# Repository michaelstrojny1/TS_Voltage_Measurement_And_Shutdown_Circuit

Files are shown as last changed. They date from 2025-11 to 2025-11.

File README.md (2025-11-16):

Built for Electric Car tractive system. Two circuits are included:
(1) Galvanically isolated low noise high voltage measurement circuit feeding voltage measurement to STM32 MCU. 
(2) Relay powered Shutdown Circuit discharging DC-Link (RC circuit initally at ~600V) to 60V in 3 seconds

Please read **Documentation.pdf** for calculations and further explanation

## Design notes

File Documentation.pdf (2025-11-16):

# TS Measurement & Discharge

Michael Strojny
Link to Altium Project (https://michael-strojny.365.altium.com/designs/B8E9C9AF-7C63-4BC2-A13C-E0917E1C21B7)

## 1.0 TS Measurement Circuit

### 1.0.1 Our Approach

The AMC1311B (https://www.ti.com/lit/ds/symlink/amc1311.pdf?HQS=dis-dk-null-digikeymode-dsf-pf-null-wwe&ts=1762965607737) takes in a voltage between 0 and 2V and outputs that voltage in differential pair form (i.e difference between pairs equals V ). Since our DC-link voltage is around , we
IN

600V
divide our voltage using a 301:1 ratio voltage divider; our top resistor is 6 MΩ and the bottom resistor is 20 kΩ. The MCU to which the differential pair feeds then re-scales the divided voltage back to the true value, “measuring” the DC-Link voltage.

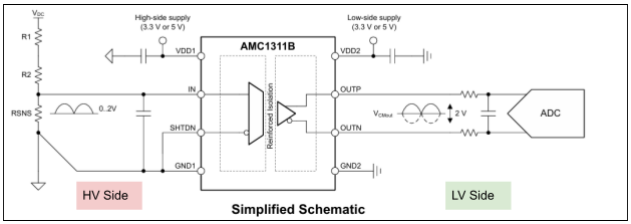
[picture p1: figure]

Figure 1 – AMC1311B + Schematic with Best Practices AMC1311B Datasheet (https://www.ti.com/lit/ds/symlink/amc1311.pdf?HQS=dis-dk-null-digikeymode-dsf-pf-null-wwe&ts=1762965607737)

The input of the AMC1311B is galvanically isolated from the output, which prevents dangerous high voltage from reaching our low voltage electronics. The AMC1311B clamps voltages above 2V. However, extra current still flows into the AMC1311B at higher input voltages. The AMC’s maximum input current is 10mA, yet the AMC impedance is ~1 gigaohm, meaning we are resilient even to large transients.

Notice that we require a 3.3 or 5V supply on both sides of the AMC1311B (pins VDD1 and VDD2). This power will come from the low voltage side. We power the high voltage side by connecting the low voltage power supply to the high voltage side using a 5VDC to 5VDC isolated converter NME0505DC. (https://www.murata.com/products/productdata/8807031111710/kdc-nme.pdf) This keeps both sides galvanically isolated. Note that the NME0505DC (https://www.murata.com/products/productdata/8807031111710/kdc-nme.pdf) requires at least 10% of its fully rated load (200 mA) to work properly.

The AMC1311B chops the input signal at a rate of 20Mhz meaning we need a couple picofarads of capacitance in parallel with the voltage divider feeding into the AMC to ensure we have enough current to supply each switch. The AMC also steals about 3.5 nA of current from our divider; it has 1 gigaohm impedance in parallel with the 20 kΩ; its effect on the voltage divider is negligible. Additional decoupling capacitors are also recommended for power supplies. See Figure 2.

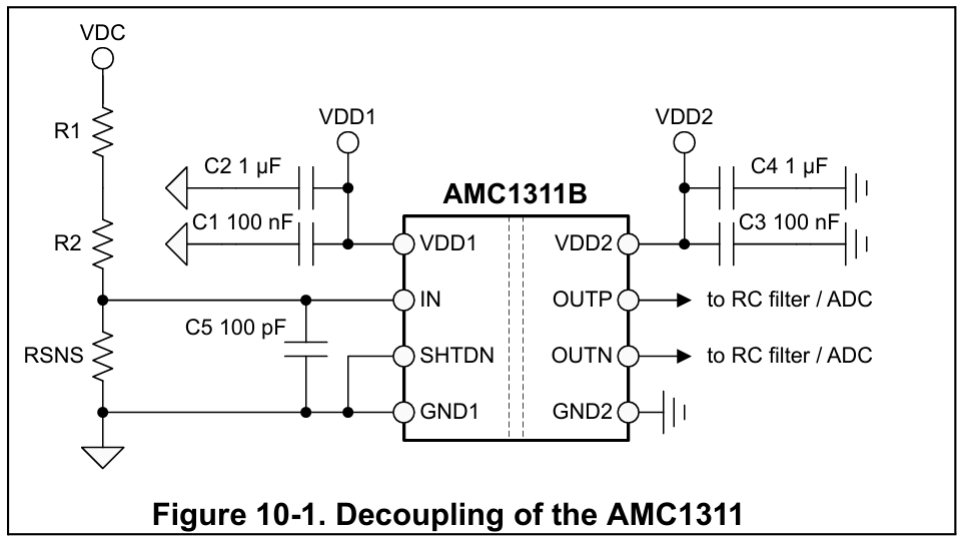
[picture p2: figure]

Figure 2 – Recommended AMC1311 Decoupling Capacitor Layout

Some STM32 MCUs accept differential pairs and some don't. If our MCU does not accept differential pairs, we can simply use an Op-Amp to get a 3.3V analog signal. See Figure 3 for an example on how to do this given by the datasheet, where “For most applications, R1 = R2 = R3 = R4 = 3.3 kΩ and C1 = C2 = 330 pF yields good performance”. More information can be found in 18-Bit, 1MSPS Data Acquisition Block (DAQ) (https://www.ti.com/lit/ug/slau515a/slau515a.pdf?ts=1763006584930)

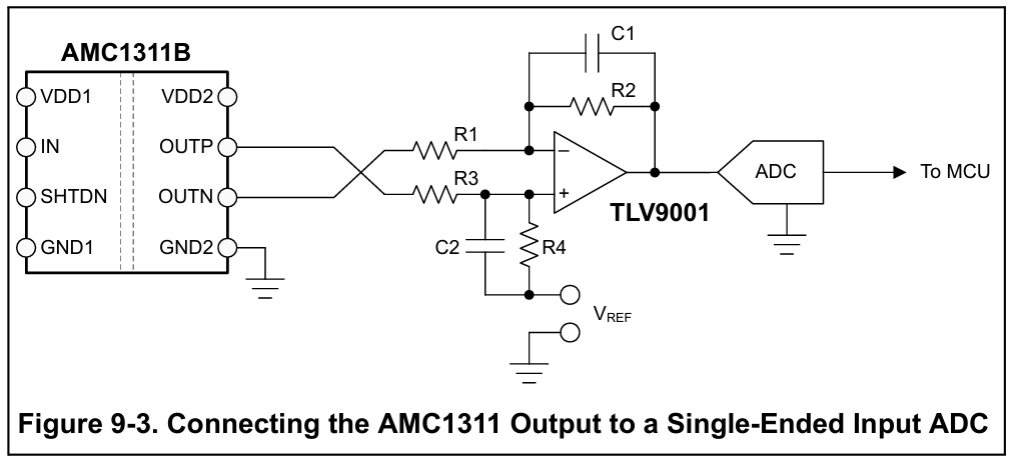
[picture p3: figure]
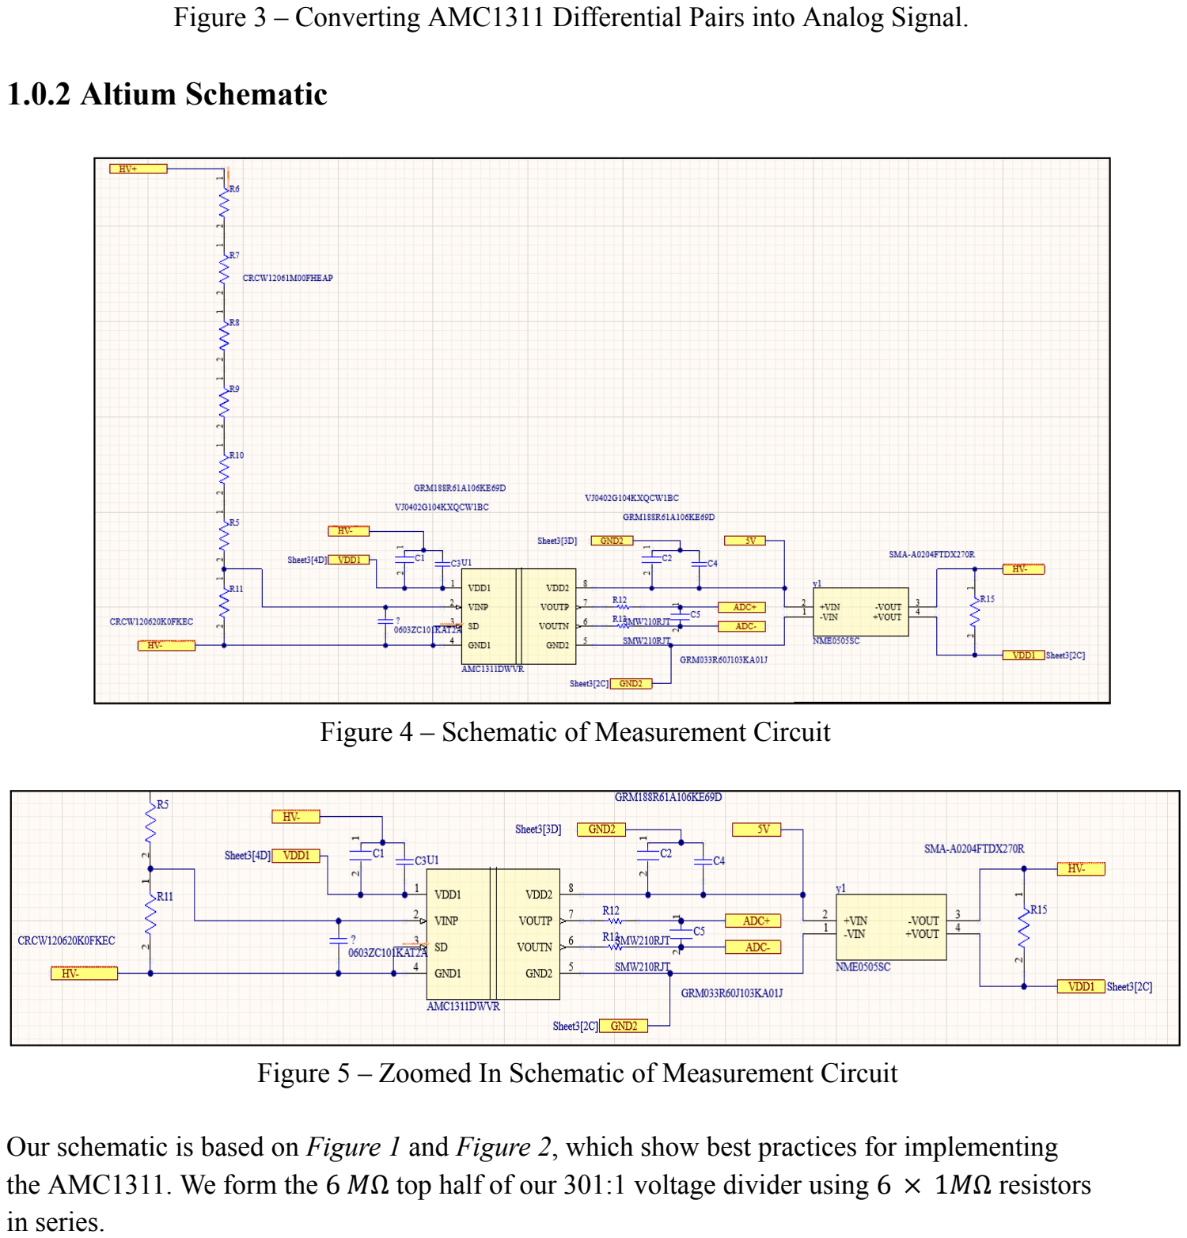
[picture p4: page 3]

Figure 3 – Converting AMC1311 Differential Pairs into Analog Signal.

### 1.0.2 Altium Schematic

Figure 4 – Schematic of Measurement Circuit

Figure 5 – Zoomed In Schematic of Measurement Circuit

Our schematic is based on Figure 1 and Figure 2, which show best practices for implementing the AMC1311. We form the 6 MΩ top half of our 301:1 voltage divider using 6 × 1MΩ resistors in series.

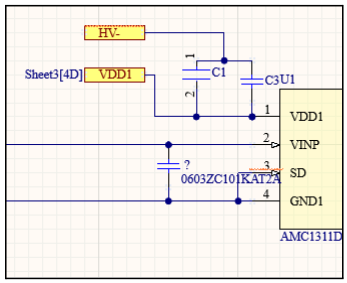
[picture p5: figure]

Figure 6 – Input of AMC1311DC

We place a capacitor between VDNP (the AMC1311 input) and its GND to ensure we can supply enough current to the 20 MHz switching of the AMC. Since our input impedance is 20 kΩ, a 100pF input capacitance would yield a 2 microsecond time constant (10 microsecond settling time) and 80 kHz cutoff (-3dB reduction that increases as frequency grows higher). This agrees with the AMC datasheet’s recommendations, which chose 100pF for a 20 kΩ input impedance as well (see Figure 2). The datasheet recommends a filter less than 1 order of magnitude of the sampling frequency (20 Mhz) so it does not interfere.

The average AMC input current is around 3. 5 nA (worst case 15 nA). The max charge drawn at
each AMC switch is | and the corresponding voltage drop
IMAX f switcℎ = | 15 nA 20 MHz = 7. 5 × 10 −16 C
across the capacitor is | which is negligible. ⁷.5×10

−16 C
100 pF = 7. 5 µV

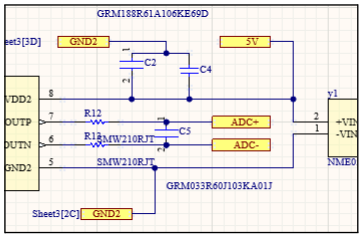
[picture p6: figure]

Figure 7 – Output of AMC1311DC

Following the Datasheet guidelines, we place a 22 nF capacitor between the AMC1311’s differential pair in order to offer a low impedance path for high frequency differential noise to equalize. We place a 20 ohm resistor on each differential pair, creating a low pass on 330 kHz. This will dampen noise but not the differential pair frequency 100-220kHz. The transfer function magnitude for 100 kHz is 0.96. The phase shift is – 15 degrees, creating a signal delay of .

θ
360

T =

15
360

1
100 kHz = 416 ns
|H(f) | =

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
100000

330000 ⎡
⎣

⎤
⎦

2

= 0. 96

θ(f) = − arctan(

f
f
c

) =− 15 deg

Common mode noise can be filtered using common mode choke, however, this is very likely overkill. Common mode amplification is much less than differential mode amplification when the differential pair is generated (ratio is 77 DB), and the signal likely won’t travel over a long distance.

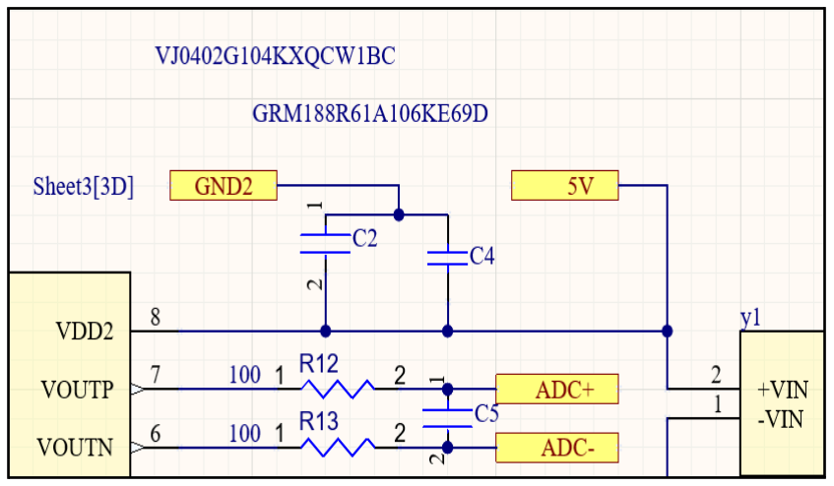
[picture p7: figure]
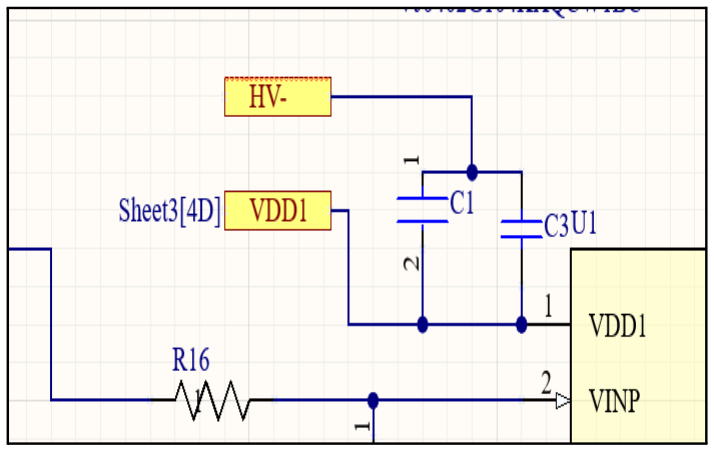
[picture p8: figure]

Figure 8 – High and Low Side Power Pins (VDD1, VDD2) of AMC1311DC

Finally, we place capacitors in parallel between low voltage supplies and ground to stabilize the power input. We use 10 µF (1-10 kHz filtering) and 0.1 µF (100+ kHz filtering) in parallel to handle a range of frequencies of noise and also have enough capacitance to supply instantaneous power.

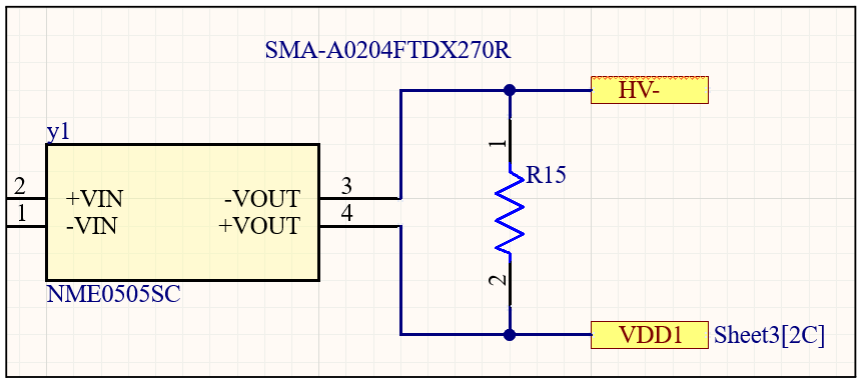
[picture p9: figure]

Figure 9 – Output of NME0505SC 5V-5V converter

Finally, recall that the NME0505DC requires at least 10% of its fully rated load (10% of 200 mA) to work properly. The AMC draws about 7.1 mA for VDD1 when supplied with 5V. We add a 270 Ohm resistor in parallel to VDD1 so that this number goes up to ~25 mA.

### 1.0.3 TS Measurement Circuit Parts & Justification

Part | Ratings | Purpose
AMC1311 (https://www.alldatasheet.com/datasheet-pdf/pdf/1002383/TI1/AMC1311.html) | Isolated input voltage to differential pair converter | 0-2 V input range with 5 kV RMS isolation barrier | Converts 0-2V signal from 600 V divider into differential signal for MCU
NME0505SC (https://datasheet.octopart.com/NME0505SC-Murata-Power-Solutions-datasheet-12516350.pdf) | Isolated 5 DC to 5 DC converter | Input 4.5–5.5 V, Output: 5 V, 200 mA. Isolation: 1 kV | Connects 3.3/5V power from low voltage side to high voltage side to power AMC
CRCW12061M00 FHEAP (https://www.digikey.com/en/products/detail/vishay-dale/CRCW12061M00FHEAP/5076755) | 1 MΩ resistor | Each is rated for 250 V, and sees 133V (max) in our circuit | 6 are used in series to get the top half of the 301:1 voltage divider
CRCW120620K0 FKEC (https://www.digikey.ca/en/products/detail/vishay-dale/CRCW120620K0FKEA/1176790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) | 20 kΩ resistor | Rated for 70V (0.25 W). Sees < 2V in our circuit. | Bottom half of the 301:1 voltage divider
VJ0402G104KX QCW1BC (https://www.bing.com/search?q=VJ0402G104KXQCW1BC&cvid=544e200ed661418b85f1903917253df5&FORM=ANAB01&PC=HCTS) | 0.1 µF capacitor | 10 V rating | High frequency denoising
GRM188R61A10 6KE69D (https://www.digikey.com/en/products/detail/murata-electronics/GRM188R61A106KE69D/5027559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) | 10 µF capacitor | 10V rating | Lower frequency denoising and current supply
0603ZC101KAT2 A (https://octopart.com/part/kyocera-avx/0603ZC101KAT2A) | 100 pF capacitor | 10 V rating | Decoupling capacitor for AMC1311 input.
C0603C223K4R AC (https://www.digikey.com/en/products/detail/kemet/C0603C223K4RACTU/411092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) | 22 nF capacitor | 16V rating | Forms a quick responding RC circuit at the IN terminal of the AMC1311. Also used as a decoupling capacitor between differential pairs of AMC1311.
SMA-A0204FTD X270R (https://www.digikey.com/en/products/detail/te-connectivity-passive-product/SMA-A0204FTDX270R/22763224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) | 270 ohm resistor | 10 V rating | In parallel with VDD1 so NME0505DC supplies sufficient current to work properly

## 2.0 Discharge Circuit

### 2.0.1 Altium Schematic

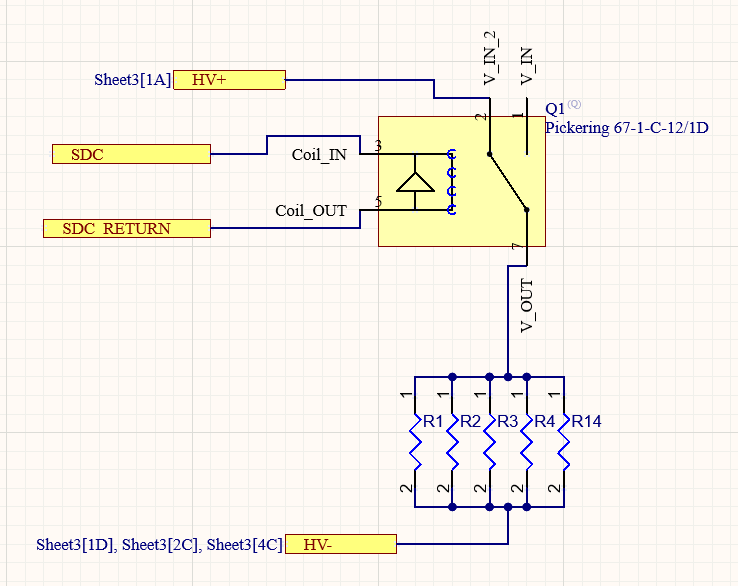
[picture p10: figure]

Figure 10 – Discharge Circuit

The five parallel resistors, RH02530K00FC02, (https://www.mouser.ca/ProductDetail/Vishay-Dale/RH02530K00FC02?qs=%2FpO%2FjbY2KwUeArnFz5wYsw%3D%3D) are rated 30 kOhm and 25 W; collectively, they form 6 kOhm of resistance. Each resistor runs at 47% of its rating at 600V. The discharge takes less than 5 seconds, and only a small amount of energy is transferred to the resistors (~20 J), making the true factor of safety much larger. Rule EV4.9.1 is not clear in which mode the circuit must be able to handle the max TS voltage permanently; our circuit passes both cases.

Our normally closed relay is the Pickering 67ES-1-C-24/1D (https://www.pickeringrelay.com/pdfs/67-68-high-voltage-reed-relays.pdf) which can handle voltages up to 2.5kV when switching and 5kV when steady. The rated current is 3A, yet, our circuit runs 0.13A at 600 volts. The shutdown circuit (SDC) powers the relay coil. The coil has a 24V limit with 18V minimum activation; we will require a voltage divider if our SDC voltage is greater than 24V as we are operating the coil continuously. Note that the Pickering has a diode between the coil terminals built in and is normally closed on Pin 2 (see Figure 11)

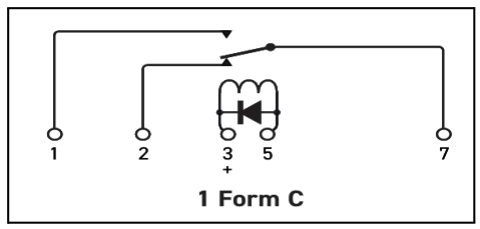
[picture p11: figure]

Figure 11 – 67ES-1-C-24/1D (https://www.pickeringrelay.com/pdfs/67-68-high-voltage-reed-relays.pdf) is normally closed on pin 2

### 2.0.3 Discharge Time

The DC link has a capacitance of 240 µF. The time constant of the shutdown circuit (τ = RC) is thus 1.44s. The time it takes to discharge to 60 V falls within the 5 second requirement:

t = τ ln(

600
60

) = 3. 0 s

## 3.0 PCB Layout

### 3.0.1 TS Measurement Circuit

Just like in a buck converter, we want low impedance between the voltage divider and
AMC1311B input as di/dt is very high due to 20 MHz switching; even nanohenries could lead to massive voltage spikes. Also, remember to use differential pair routing for the differential pairs OUTP and OUTN. Finally, there must be no conductive material beside and below the AMC.

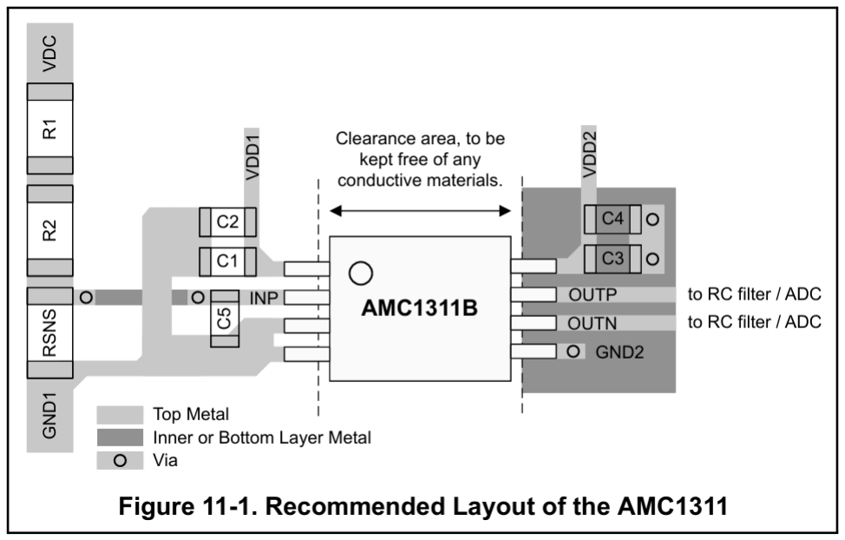
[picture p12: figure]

Figure 12 – Recommended AMC1311 Layout

The NME0505DC is a resonant converter and is galvanically isolated, so all “AMC1311B ” ytrouting/placement rules apply to this component also. Its switching frequency is 110 kHz.

### 3.0.2 Discharge Circuit

There isn’t much to consider when placing+routing the shutdown circuit. We see 600V passing through 6 kOhm, yielding 10mA, meaning that any trace width works. Our lower limit is 1 mil width for 1oz copper if we wish to keep temperature rise under 10K; Trace Width Calculator. (https://www.advancedpcb.com/en-us/tools/trace-width-calculator/)
